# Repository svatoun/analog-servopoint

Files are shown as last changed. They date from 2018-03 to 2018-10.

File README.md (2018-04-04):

# analog-servopoint

Analog-servopoint je zařízení určené k ovládání servo a spínaných (zap/vyp) výstupů pro analogově řízený model železnice. Základní deska má tyto vstupy a výstupy:

1. Vstup z maticové klávesnice 4x4 tlačítek. Funguje jak pro spínací mžiková tlačítka, tak pro přepínací tlačítka. U přepínacích tlačítek může mít význam přepnutí do obou poloh.
2. Ovládání až 8 modelářských serv. 
3. 8 tranzistorem spínaných výstupů, zatížení cca 500mA/výstup, celkem 2,5A

Software poskytuje následující funkce:

### Ovládání serva
1. Určení 2 poloh (levá, pravá) pro každé servo.
2. Určení rychlosti přestavování serva.
3. Interaktivní kalibrace serva
4. Plynulé přestavení serva do předdefinované pravé/levé polohy, nebo na libovolný úhel
5. Postupné spínaní serv, eliminaci proudové špičky, omezení zákmitu serva
6. "Ohlas" polohy serva na definovaném spínaném výstupu (ON/OFF)
7. Přestavování 2 serv najednou

### Ovládání jednotlivých výstupů
1. Zapnutí, vypnutí
2. Pulz 300ms, nebo zadané délky
3. (stále ve vývoji) Blikání s určenou dobou zapnutí a prodlevy. Blikání v protifázi.
4. Napájení tranzistorového pole lze volit jumperem, +5V nebo napětí zdroje.

### Reakce na tlačítka
Tlačítka se čtou po sloupcích, v případě přepinačů je nutné zařadit do matice diody.
1. Přiřazení sekvencí pokynů pro serva a spínané výstupy (max 10 akcí)
2. Spuštění sekvence při stisku, rozepnutí tlačítka nebo obojím
3. Vyčkání přestavení serva, nebo provedení několika akcí najednou
4. Při rozepnutí tlačítka je možné celou posloupnost akcí vrátit nebo přerušit
5. Volitelné prodlevy mezi akcemi
6. Postupné vykonání akcí pro tlačítka stisknutá najednou či v těsném sledu (max 20)

### Nastavení, komunikace
1. Deska se nastavuje a může komunikovat pomocí mikroUSB rozhraní Arduina. 
2. Je možné přímo přikazovat jednotlivé akce (spínání, nastavení serva)
3. Jednoduchý textový výpis konfigurace pro zálohování
4. Upgrade obslužného SW - pomocí Arduino IDE

Podrobnosti viz [Wiki](https://github.com/svatoun/analog-servopoint/wiki/)

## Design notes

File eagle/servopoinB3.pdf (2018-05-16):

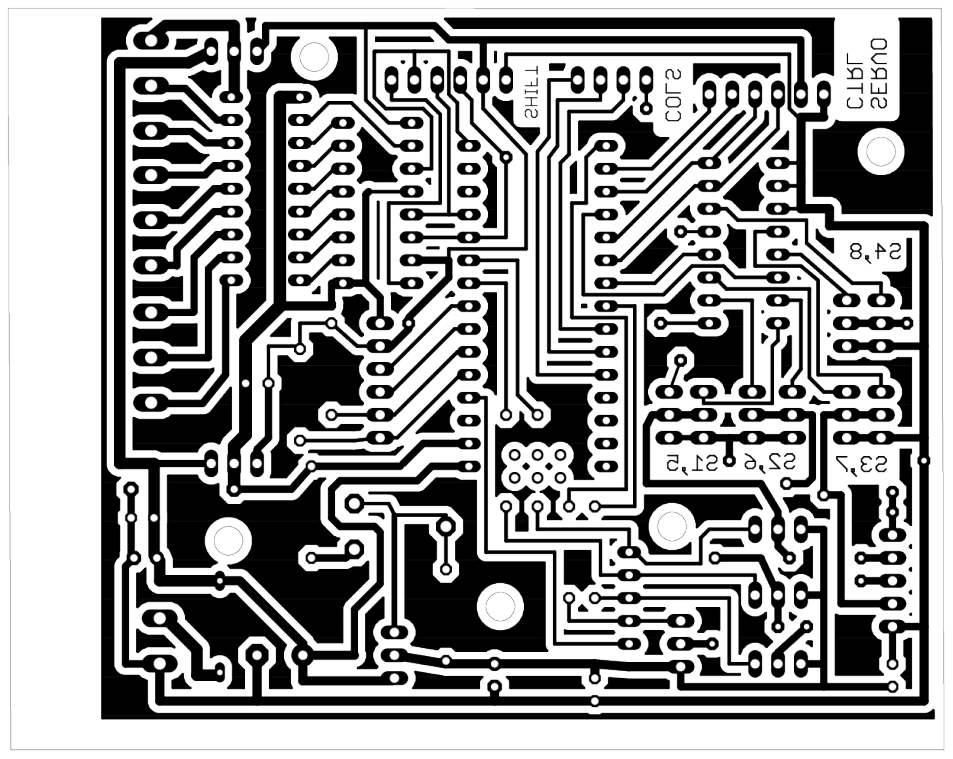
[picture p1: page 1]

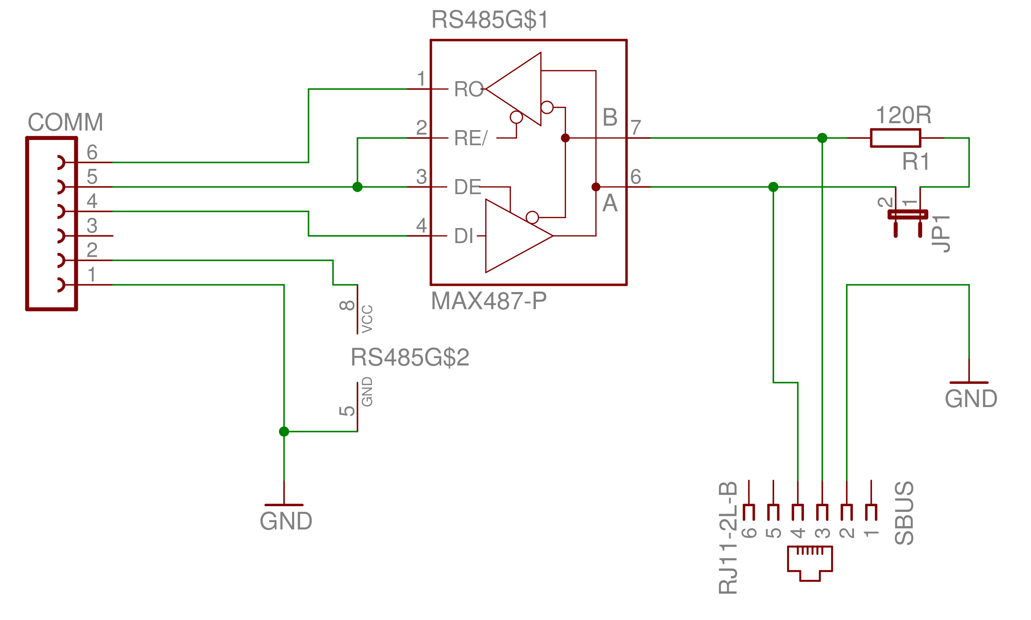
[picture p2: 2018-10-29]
eagle/tco-commheader-pins-schema.png

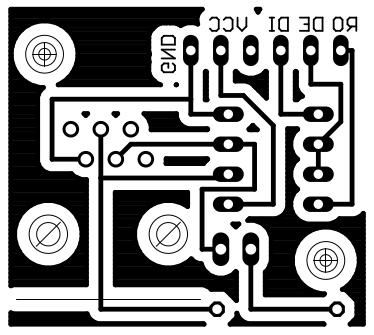
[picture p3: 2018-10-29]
eagle/tco-commheader-pins.png

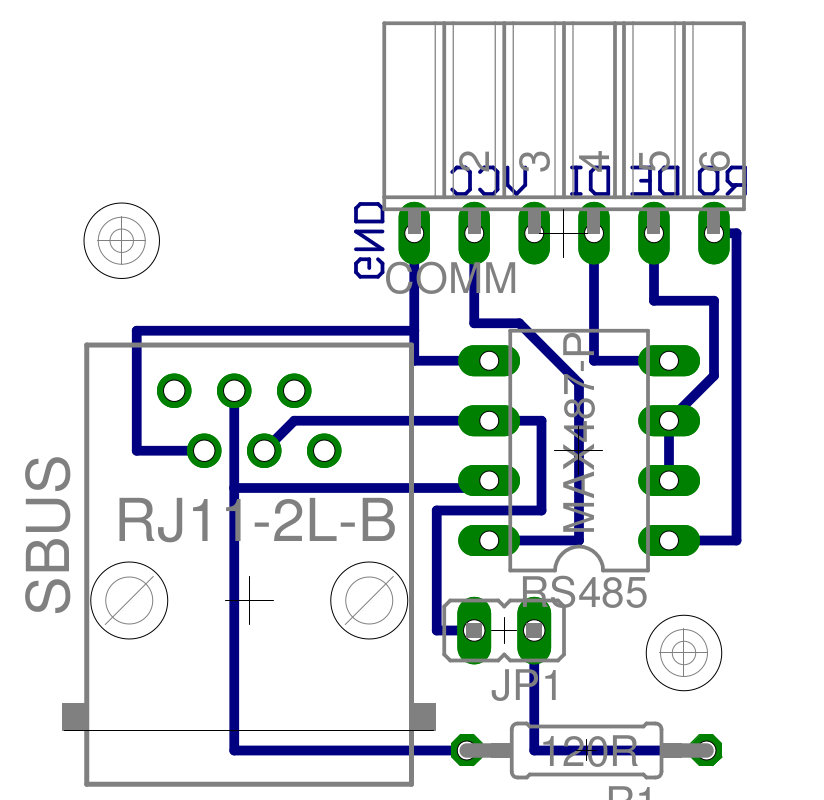
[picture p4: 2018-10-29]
eagle/tco-commheader-pins-osaz.png

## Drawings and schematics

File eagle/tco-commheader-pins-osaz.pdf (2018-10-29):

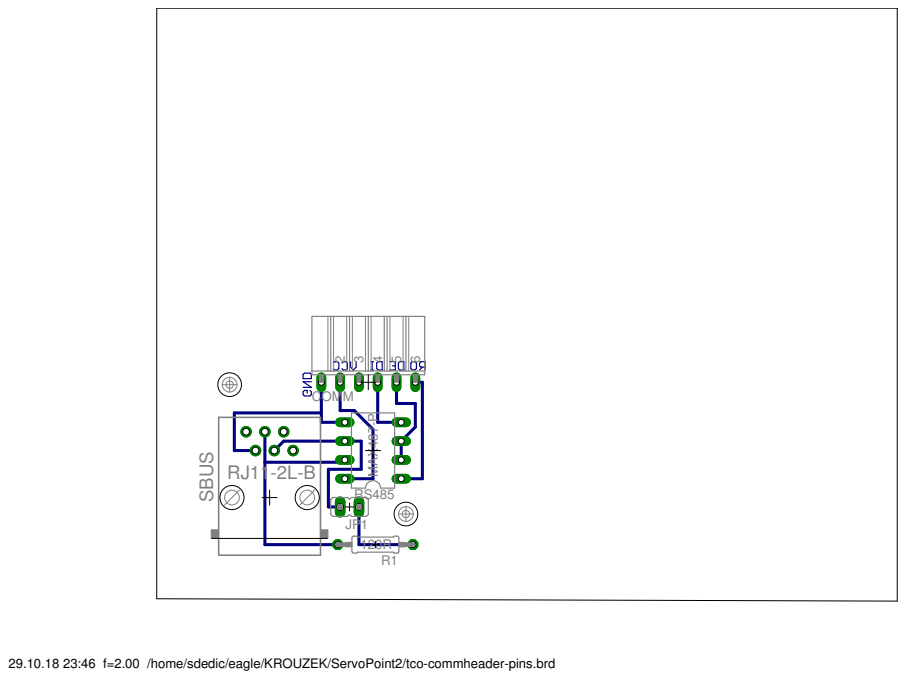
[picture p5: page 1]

29.10.18 23:46 f=2.00 /home/sdedic/eagle/KROUZEK/ServoPoint2/tco-commheader-pins.brd

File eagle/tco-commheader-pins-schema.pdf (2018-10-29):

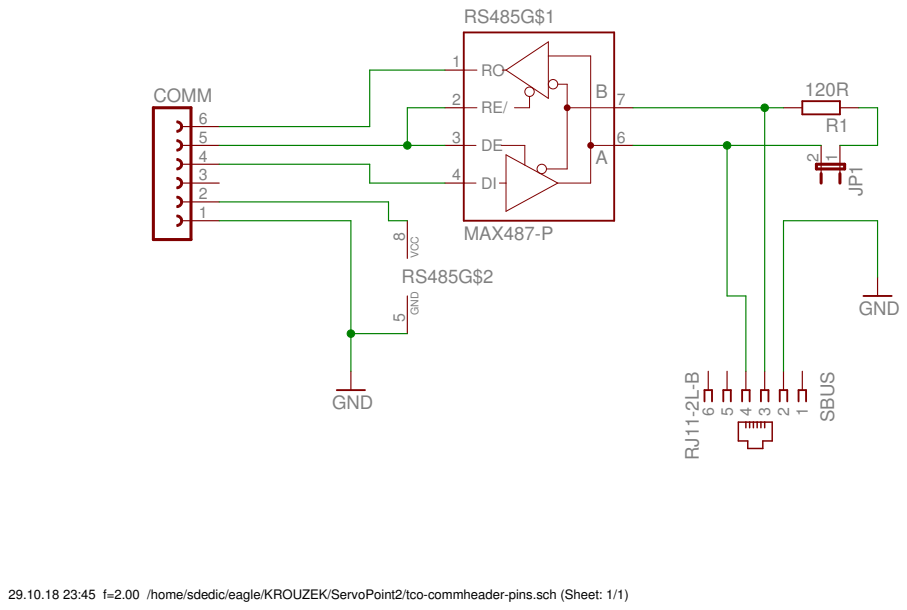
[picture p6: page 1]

29.10.18 23:45 f=2.00 /home/sdedic/eagle/KROUZEK/ServoPoint2/tco-commheader-pins.sch (Sheet: 1/1)

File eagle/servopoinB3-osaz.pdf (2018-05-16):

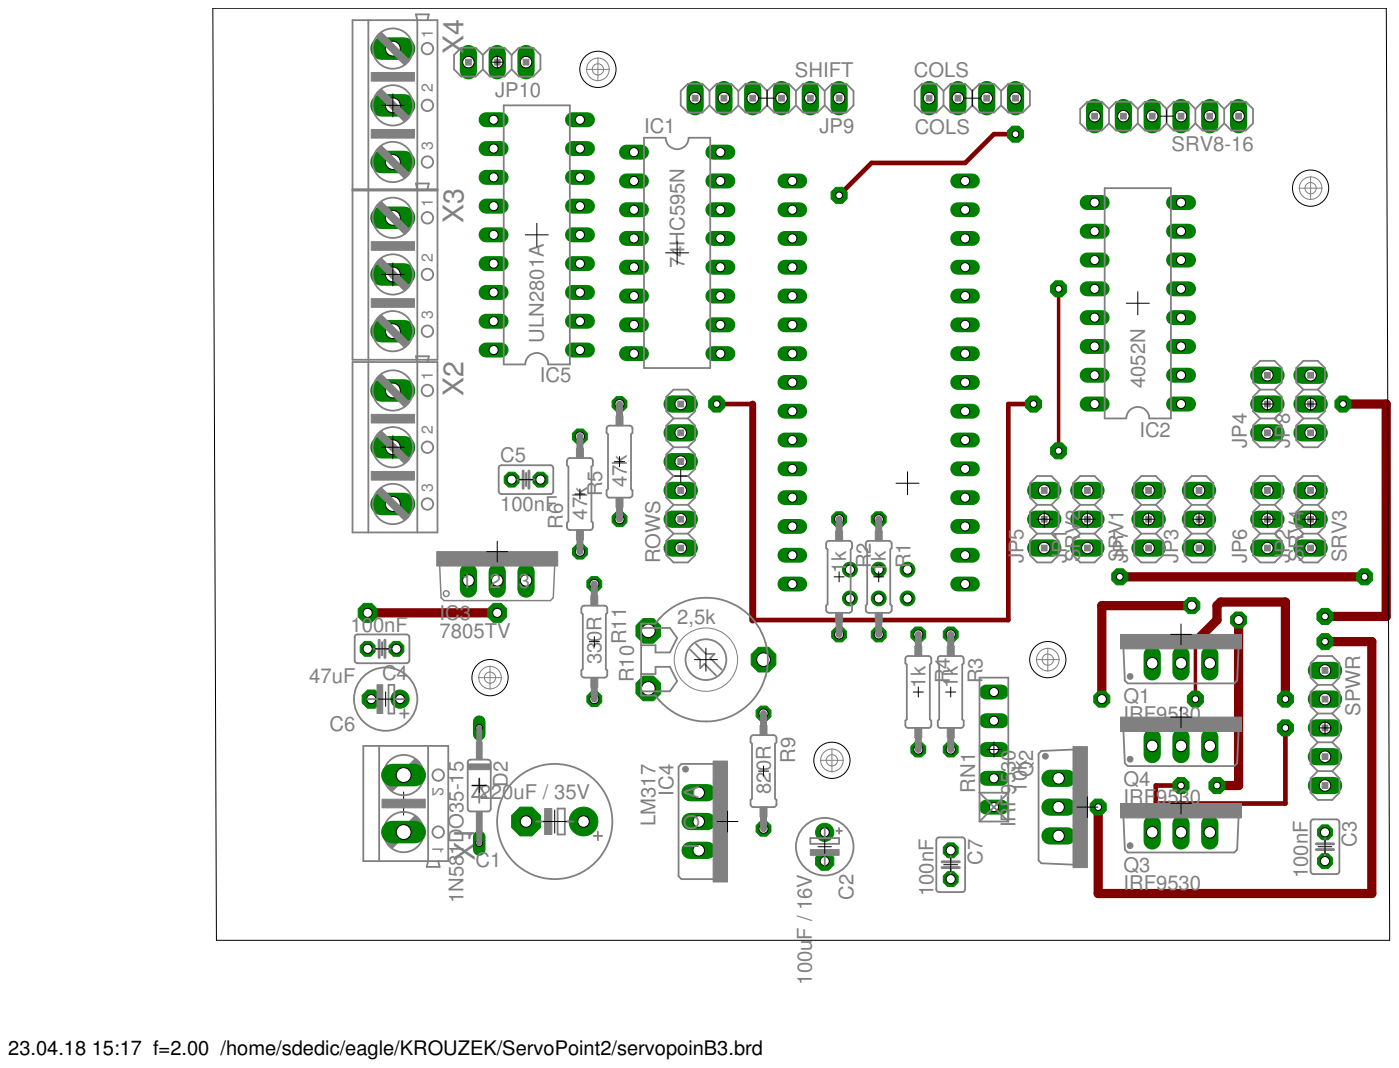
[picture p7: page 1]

23.04.18 15:17 f=2.00 /home/sdedic/eagle/KROUZEK/ServoPoint2/servopoinB3.brd

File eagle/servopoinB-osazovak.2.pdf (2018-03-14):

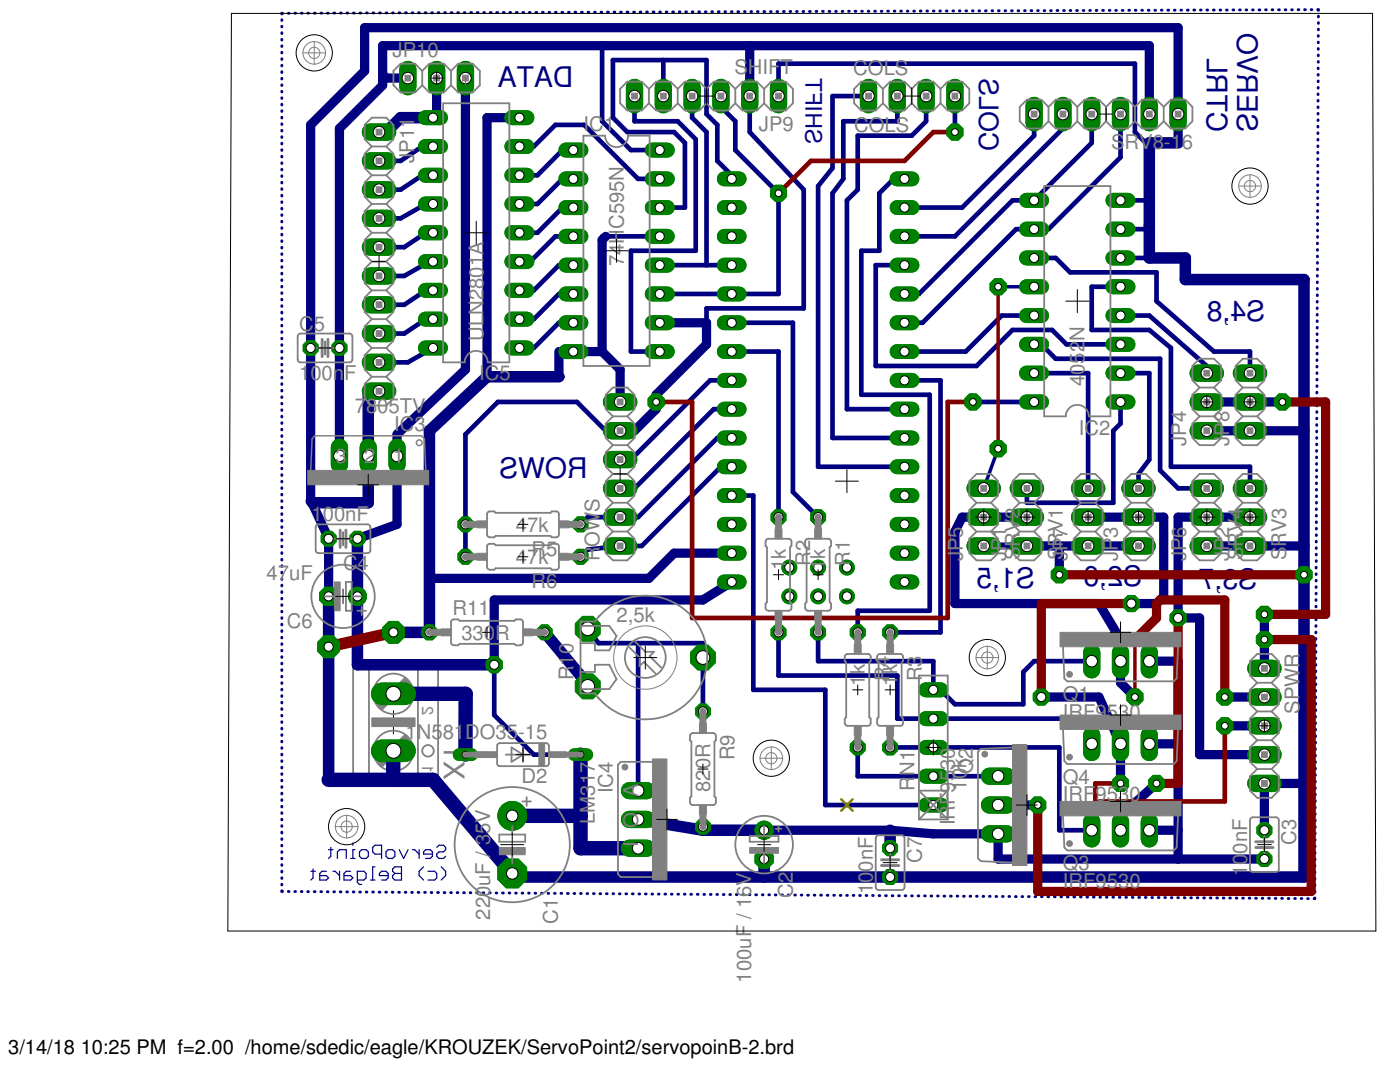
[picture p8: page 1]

3/14/18 10:25 PM f=2.00 /home/sdedic/eagle/KROUZEK/ServoPoint2/servopoinB-2.brd

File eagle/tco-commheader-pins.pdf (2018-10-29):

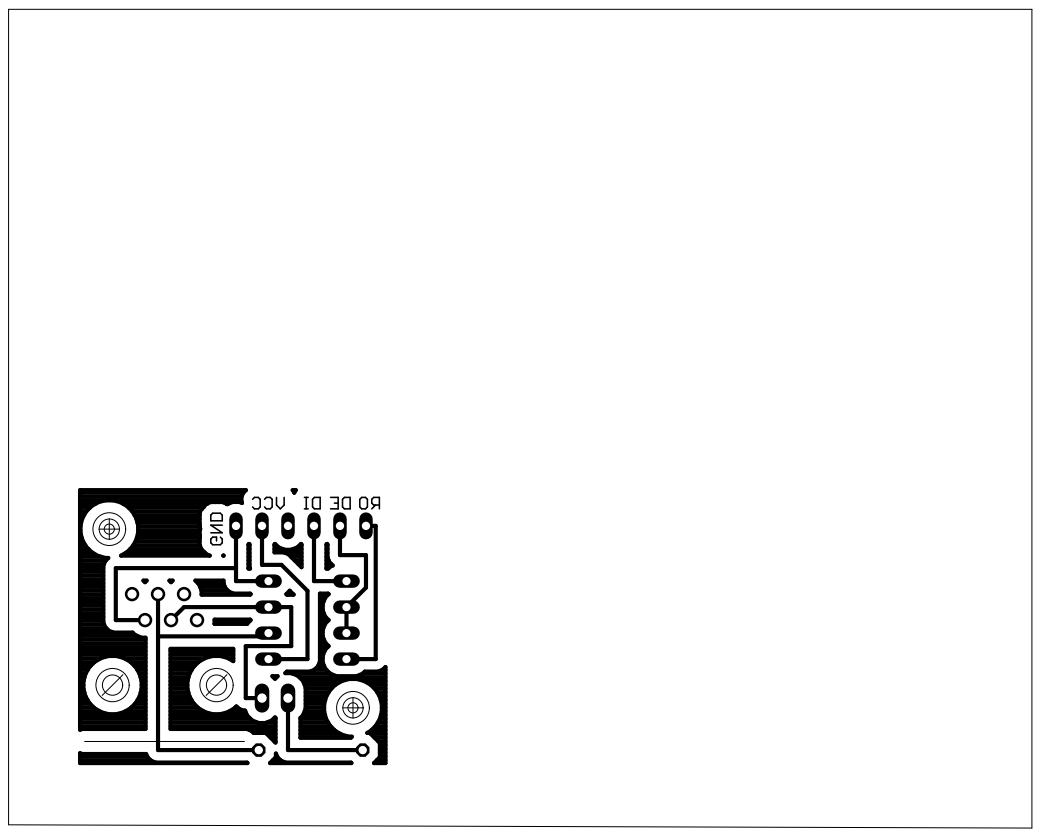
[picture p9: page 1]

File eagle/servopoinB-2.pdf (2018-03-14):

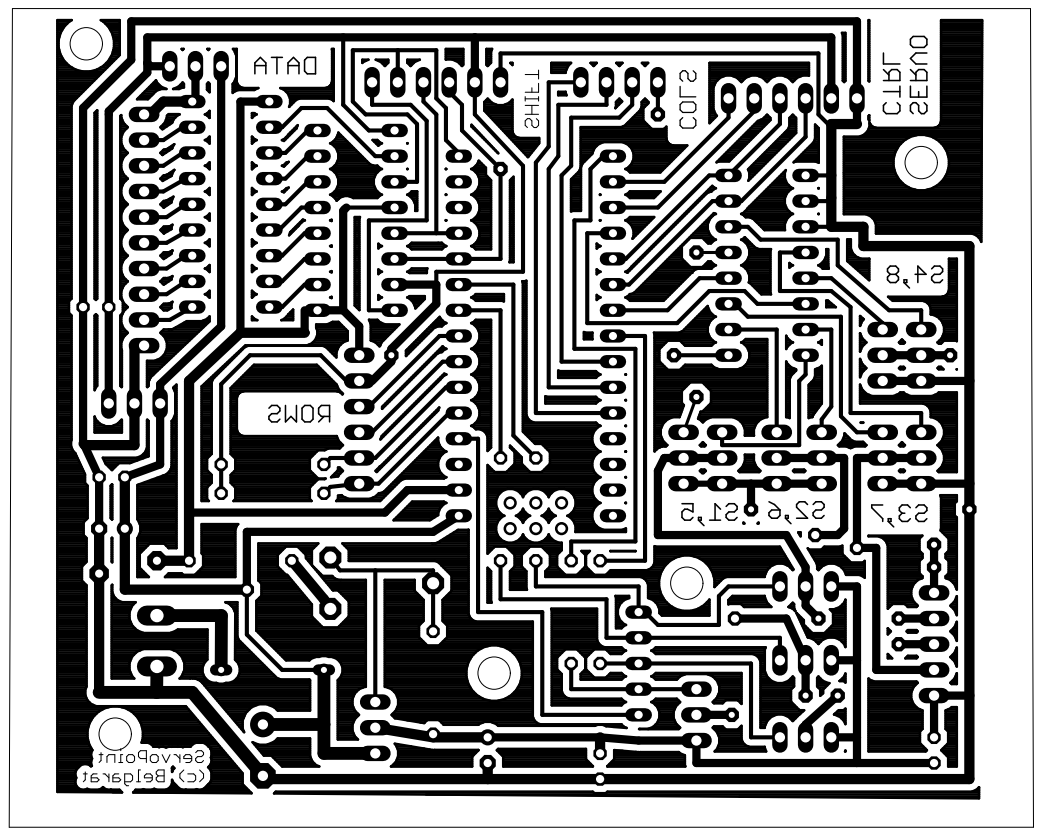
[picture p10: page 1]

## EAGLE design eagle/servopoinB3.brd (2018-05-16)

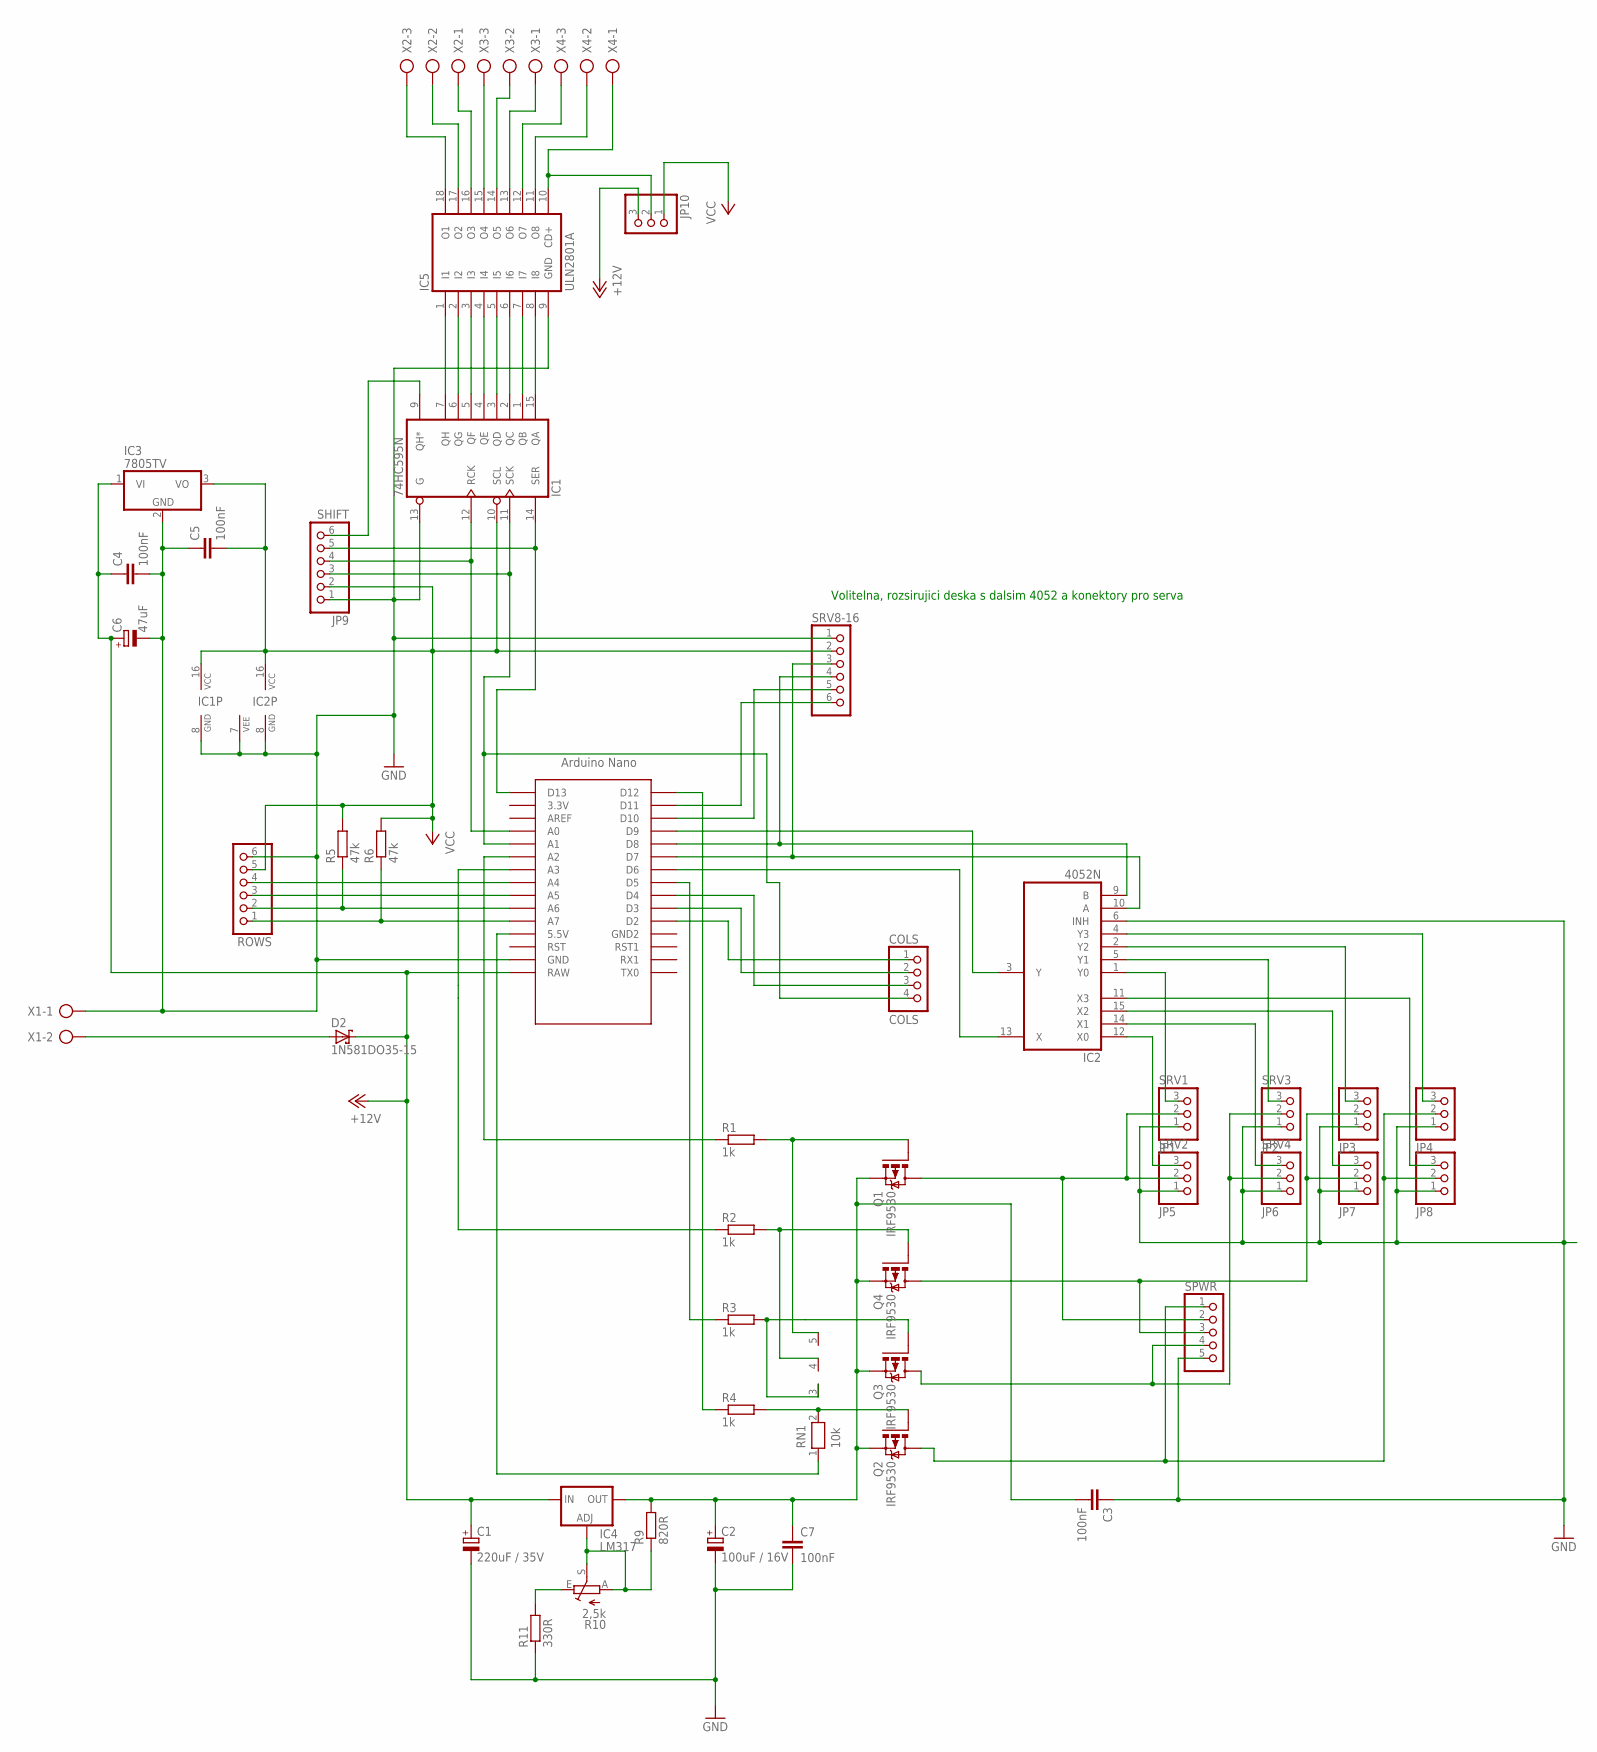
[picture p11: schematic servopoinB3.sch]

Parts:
C1: 220uF / 35V; E5-10,5
C2: 100uF / 16V; E2,5-5
C3, C4, C5, C7: 100nF; C025-025X050
C6: 47uF; E2,5-6
COLS: COLS; 1X04
D2: 1N581DO35-15; DO35-10
IC1: 74HC595N; DIL16
IC2: 4052N; DIL16
IC3: 7805TV; TO220V
IC4: LM317; 317TS
IC5: ULN2801A; DIL18
JP1: SRV1; 1X03
JP2: SRV3; 1X03
JP3, JP4, JP7, JP8, JP10: PINHD-1X3; 1X03
JP5: SRV2; 1X03
JP6: SRV4; 1X03
JP9: SHIFT; 1X06
Q1, Q2, Q3, Q4: IRF9530; TO220BV
R1, R2, R3, R4: 1k; 0207/10
R5, R6: 47k; 0207/10
R9: 820R; 0207/10
R10: 2,5k; LI10
R11: 330R; 0207/10
RN1: 10k; RN-5
ROWS: PINHD-1X6; 1X06
SPWR: PINHD-1X5; 1X05
SRV8-16: PINHD-1X6; 1X06
U$1: NANO
X1: AK500/2
X2, X3, X4: AK500/3

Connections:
+12V: C1.+, C4.1, C6.+, D2.C, IC3.1 (VI), IC4.3 (IN), JP10.3, U$1.RAW
GND: C1.-, C2.-, C3.1, C4.2, C5.1, C6.-, C7.2, IC1.8 (GND), IC1.13 (G), IC2.6 (INH), IC2.7 (VEE), IC2.8 (GND), IC3.2 (GND), IC5.9 (GND), JP1.1, JP2.1, JP3.1, JP4.1, JP5.1, JP6.1, JP7.1, JP8.1, JP9.1, R11.1, ROWS.6, SPWR.5, SRV8-16.1, U$1.GND, X1.1
unnamed: IC2.13 (X), U$1.D6
unnamed: IC2.3 (Y), U$1.D9
unnamed: IC1.15 (QA), IC5.8 (I8)
unnamed: COLS.4, IC1.11 (SCK), JP9.3, U$1.A1
unnamed: IC2.12 (X0), JP5.3
unnamed: IC2.1 (Y0), JP1.3
unnamed: IC2.14 (X1), JP6.3
unnamed: IC2.5 (Y1), JP2.3
unnamed: IC2.15 (X2), JP7.3
unnamed: IC2.2 (Y2), JP3.3
unnamed: IC2.11 (X3), JP8.3
unnamed: IC2.4 (Y3), JP4.3
unnamed: Q1.G, R1.2, RN1.5
unnamed: JP2.2, JP6.2, Q3.D, SPWR.4
unnamed: R6.1, ROWS.1, U$1.A7
unnamed: R2.1, U$1.A3
unnamed: Q4.G, R2.2, RN1.4
unnamed: R3.1, U$1.D5
unnamed: Q3.G, R3.2, RN1.3
unnamed: RN1.1, U$1.5V (5.5V)
unnamed: Q2.G, R4.2, RN1.2
unnamed: JP3.2, JP7.2, Q4.D, SPWR.3
unnamed: R4.1, U$1.D12
unnamed: R1.1, U$1.A2
unnamed: D2.A, X1.2
unnamed: ROWS.4, U$1.A4
unnamed: ROWS.3, U$1.A5
unnamed: R5.1, ROWS.2, U$1.A6
unnamed: SRV8-16.6, U$1.D11
unnamed: COLS.2, U$1.D3
unnamed: COLS.3, U$1.D4
unnamed: COLS.1, U$1.D2
unnamed: SRV8-16.5, U$1.D10
unnamed: IC1.14 (SER), JP9.5, U$1.D13
unnamed: IC1.1 (QB), IC5.7 (I7)
unnamed: IC1.9 (QH*), JP9.6
unnamed: IC1.12 (RCK), JP9.4, U$1.A0
unnamed: C2.+, C3.2, C7.1, IC4.2 (OUT), Q1.S, Q2.S, Q3.S, Q4.S, R9.2
unnamed: IC5.10 (CD+), JP10.2, X4.1
unnamed: IC1.2 (QC), IC5.6 (I6)
unnamed: IC1.3 (QD), IC5.5 (I5)
unnamed: IC1.4 (QE), IC5.4 (I4)
unnamed: IC1.5 (QF), IC5.3 (I3)
unnamed: IC1.6 (QG), IC5.2 (I2)
unnamed: IC1.7 (QH), IC5.1 (I1)
unnamed: IC5.18 (O1), X2.3
unnamed: IC4.1 (ADJ), R9.1, R10.A, R10.S
unnamed: R10.E, R11.2
unnamed: IC5.17 (O2), X2.2
unnamed: JP1.2, JP5.2, Q1.D, SPWR.2
unnamed: IC5.16 (O3), X2.1
unnamed: JP4.2, JP8.2, Q2.D, SPWR.1
unnamed: IC5.15 (O4), X3.3
unnamed: IC5.14 (O5), X3.2
unnamed: IC5.13 (O6), X3.1
unnamed: IC5.12 (O7), X4.3
unnamed: IC5.11 (O8), X4.2
unnamed: IC2.9 (B), SRV8-16.4, U$1.D8
unnamed: IC2.10 (A), SRV8-16.3, U$1.D7
VCC: C5.2, IC1.10 (SCL), IC1.16 (VCC), IC2.16 (VCC), IC3.3 (VO), JP9.2, JP10.1, R5.2, R6.2, ROWS.5, SRV8-16.2

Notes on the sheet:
Volitelna, rozsirujici deska s dalsim 4052 a konektory pro serva

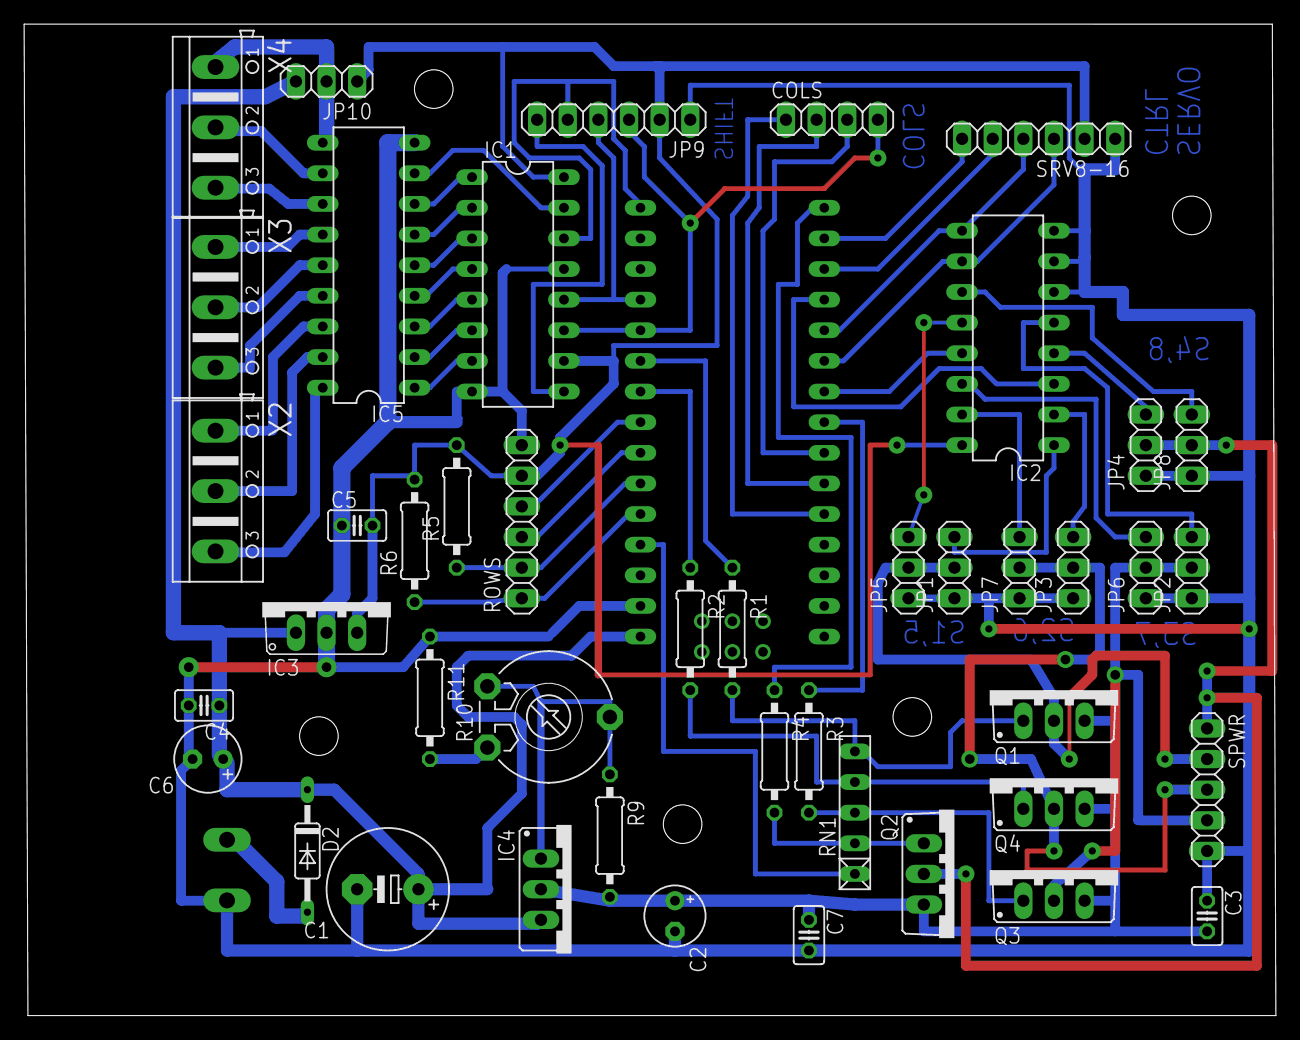
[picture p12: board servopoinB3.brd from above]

Board: 2 copper layers, 103.8 x 82.2 mm, 46 parts (1 on the bottom side), 62 nets.

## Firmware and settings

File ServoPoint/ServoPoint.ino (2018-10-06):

#ifdef NEO
#include <NeoSWSerial.h>
#else
#include <SoftwareSerial.h>
#endif

#include "RS485Frame.h"
#undef SOFTWARE_SERVO

#define DEBUG

#include <EEPROM.h>

#ifdef SOFTWARE_SERVO
#include <SoftwareServo.h>
#define Servo SoftwareServo
#else 
#include <Servo.h>
#endif

#include "Common.h"

ModuleChain* ModuleChain::head;

byte keyStateTriggered[(maxId + 7) / 8];
byte keyState[(maxId + 7) / 8];

Command commands[MAX_COMMANDS];

char printBuffer[50];

/**
   Serves to build up a new command during setup. Takes priority over any actions
*/
Action  newCommand[newCommandPartMax];


//ModuleChain *modules;

/**
   The current number of milliseconds; read at the start of the loop().
*/
long currentMillis;

Output output;
Executor executor;

char currentKey;
uint8_t * heapptr, * stackptr;
/*
void check_mem() {
  stackptr = (uint8_t *)malloc(4);          // use stackptr temporarily
  heapptr = stackptr;                     // save value of heap pointer
  free(stackptr);      // free up the memory again (sets stackptr to 0)
  stackptr =  (uint8_t *)(SP);           // save value of stack pointer
}
*/

int freeRam ()
{
  extern int __heap_start, *__brkval;
  int v;
  return (int) &v - (__brkval == 0 ? (int) &__heap_start : (int) __brkval);
}

void clearNewCommand() {
//  check_mem();
  if (debugControl) {
    Serial.println(F("Clearing new command"));
  }
  executor.clear(true);
  for (Action* a = newCommand; a < (newCommand + newCommandPartMax); a++) {
    a->init();
  }
}

int addNewCommand(const Action& t) {
  if (debugControl) {
    Serial.print(F("Adding action command "));
    Serial.print(F("Source: ")); Serial.print((int)&t, HEX);
    Serial.print(t.command);
    Serial.print(F(", data = "));
    Serial.println(t.data, HEX);
  }
  Action* prev = newCommand;
  for (Action* pa = newCommand; pa < (newCommand + newCommandPartMax); pa++) {
    Action& a = *pa;
    if (a.isEmpty()) {
      a = t;
      if (debugControl) {
        Serial.print(F("Added at position"));
        Serial.print((pa - newCommand));
        Serial.print(F(" = "));
        Serial.print((int)&a, HEX);
        Serial.print(F(":"));
        Serial.print(a.command);
        Serial.print(F(", data = "));
        Serial.println(a.data, HEX);
      }
      prev->notLast();
      a.makeLast();
      return (pa - newCommand);
    }
  }
  return -1;
}


////////////////////////////////////////////////////////////////////////////////////////////////////////////////////
// ACK / status LED handling
const int* blinkPtr = NULL;
long blinkLastMillis;
byte pos = 0;
boolean ackLedState = false;
byte pulseCount = 0;

const int blinkShort[] = { 250, 250, 0 };   // blink once, short
const int blinkLong[] = { 500, 0 };
const int blinkReject[] = { 250, 250, 250, 250, 0 };
const int blinkSave[] = { 250, 250, 250, 250, 250, 250, 500, 0 };


void makeLedAck(const int *  ledSequence) {
  blinkPtr = ledSequence;
  pos = 0;
  ackLedState = 1;
  blinkLastMillis = millis();
  digitalWrite(LED_ACK, HIGH);
  if (debugControl) {
    Serial.print(F("LED ACK: ")); Serial.println(blinkPtr[pos]);
  }
}

void handleAckLed() {
  if (blinkPtr == NULL) {
    return;
  }
  long t = millis();
  long l = t - blinkLastMillis;
  if (l < *blinkPtr) {
    return;
  }
  blinkLastMillis = t;
  blinkPtr++;
  if (debugControl) {
    Serial.print(F("Next ACK time: ")); Serial.println(*blinkPtr);
  }
  if (*blinkPtr == 0) {
    ackLedState = 0;
    digitalWrite(LED_ACK, LOW);
    if (pulseCount > 0) {
      pulseCount--;
      makeLedAck(&blinkShort[0]);
    } else {
      if (debugControl) {
        Serial.println(F("ACK done"));
      }
      blinkPtr = NULL;
      blinkLastMillis = -1;
    }
    return;
  }
  ackLedState = !ackLedState;
  digitalWrite(LED_ACK, ackLedState ? HIGH : LOW);
}

//////////////////////////////////////////////////////////////////////////

void initializeHW() {
    Serial.begin(115200);
//  Serial.begin(57600);
  // put your setup code here, to run once:
  pinMode(LED_ACK, OUTPUT);
  digitalWrite(LED_ACK, LOW);
  analogReference(DEFAULT);

  Serial.println(COPYRIGHT);
}

void checkInitEEPROM() {
  int savedVer = EEPROM.read(eeaddr_version);
  if (savedVer == CURRENT_DATA_VERSION) {
    return;
  }
  Serial.println(F("Obsolete EEPROM, reinitializing"));
  ModuleChain::invokeAll(ModuleCmd::reset);
  ModuleChain::invokeAll(ModuleCmd::eepromSave);
  EEPROM.write(eeaddr_version, CURRENT_DATA_VERSION);
}

void setup() {
  initializeHW();
  checkInitEEPROM();

  bootProcessors();
  
  ModuleChain::invokeAll(ModuleCmd::initialize);
  
  //  initializeTables();
  for (int i = 0; i < sizeof(keyState); i++) {
    keyState[i] = 0;
    keyStateTriggered[i] = 0;
  }

  // initial load of key / switch positions
//  enterSetup();

  Serial.print(F("Size of commands: ")); Serial.println(sizeof(commands));
  Serial.print(F("Size of executors: ")); Serial.println(sizeof(Executor) + sizeof(ServoProcessor));
  Serial.print(F("Size of actions: ")); Serial.println(sizeof(Action) * MAX_ACTIONS);

  registerLineCommand("SAV", &saveHandler);

  printPrompt();
}

/**
   Writes a block of data into the EEPROM, followed by a checksum
*/
void eeBlockWrite(byte magic, int eeaddr, const void* address, int size) {
  if (debugControl) {
    Serial.print(F("Writing EEPROM ")); Serial.print(eeaddr, HEX); Serial.print(F(":")); Serial.print(size); Serial.print(F(", source: ")); Serial.println((int)address, HEX);
  }
  const byte *ptr = (const byte*) address;
  byte hash = magic;
  EEPROM.write(eeaddr, magic);
  eeaddr++;
  for (; size > 0; size--) {
    byte b = *ptr;
    EEPROM.write(eeaddr, b);
    ptr++;
    eeaddr++;
    hash = hash ^ b;
  }
  EEPROM.write(eeaddr, hash);
}

/**
   Reads block of data from the EEPROM, but only if the checksum of
   that data is correct.
*/
boolean eeBlockRead(byte magic, int eeaddr, void* address, int size) {
  if (debugControl) {
    Serial.print(F("Reading EEPROM ")); Serial.print(eeaddr, HEX); Serial.print(F(":")); Serial.print(size); Serial.print(F(", dest: ")); Serial.println((int)address, HEX);
  }
  int a = eeaddr;
  byte hash = magic;
  byte x;
  boolean allNull = true;
  x = EEPROM.read(a);
  if (x != magic) {
    if (debugControl) {
      Serial.println(F("No magic header found"));
    }
    return false;
  }
  a++;
  for (int i = 0; i < size; i++, a++) {
    x = EEPROM.read(a);
    if (x != 0) {
      allNull = false;
    }
    hash = hash ^ x;
  }
  x = EEPROM.read(a);
  if (hash != x || allNull) {
    if (debugControl) {
      Serial.println(F("Checksum does not match"));
    }
    return false;
  }

  a = eeaddr + 1;
  byte *ptr = (byte*) address;
  for (int i = 0; i < size; i++, a++) {
    x = EEPROM.read(a);
    *ptr = x;
    ptr++;
  }
}

void primeKeyChange(byte k) {
  if (k >= maxId) {
    return;
  }
  bitfieldWrite(keyStateTriggered, k, true); 
}

char getKeyChange(byte k) {
  if (k >= maxId) {
    return -1;
  }
  if (bitfieldRead(keyStateTriggered, k)) {
    return -1;
  }
  return bitfieldRead(keyState, k) ? 1 : 0;
}

bool isKeyPressed(byte k) {
  if (k >= maxId) {
    return false;
  }
  return bitfieldRead(keyState, k);
}

bool setKeyPressed(int k, bool val) {
  bitfieldWrite(keyState, k, val);
  bitfieldWrite(keyStateTriggered, k, false);
}

void processKey(int k, boolean pressed) {
  setKeyPressed(k, pressed);
  Command::processAll(k, pressed);
}

/*
void processKeyCallback(const Key2& k, char c) {
    if (setupActive) {
      return;
    }
    if (debugInput) {
      Serial.println(F("Key state changed"));
    }
    if (k.kstate == IDLE || k.kstate == HOLD) {
      // ignore hold / idle
      return;
    }
    boolean pressed = (k.kstate  == PRESSED);
    int ch = keypad.getChar(k);
    Serial.print(F("Processing key: #")); Serial.print(ch);
    if (pressed) {
      Serial.println(F(" DOWN"));
    } else {
      Serial.println(F(" UP"));
    }
    processKey(ch - 1, pressed);
}
*/

void loop() {
  currentMillis = millis();
  // pressedKey = keypad.getKey();

  if (setupActive) {
    setupLoop();
  }
  scheduler.schedulerTick();
  handleAckLed();
  executor.process();
  ModuleChain::invokeAll(ModuleCmd::periodic);
  // explicit, at the end
  output.commit();
  processReceivedCommand();
}


const int blinkSetup[] = { 500, 250, 500, 250, 500, 250, 0 };
const int blinkError[] = { 1000, 250, 1000, 250, 0 };


void saveHandler() {
  ModuleChain::invokeAll(ModuleCmd::eepromSave);
}

int defineCommand(const Command& def, int no) {
  if (no >= 0) {
    if (no >= MAX_COMMANDS) {
      return -1;
    }
  } else {
    for (const Command* ptr = commands; ptr < commands + MAX_COMMANDS; ptr++) {
      if (ptr->available()) {
        no = (ptr - commands);
        break;
      }
    }
  }
  if (no == -1) {
    if (debugCommands) {
      Serial.println(F("No free slots"));
    }
    return -1;
  }
  Command& c = commands[no];
  if (!c.available()) {
      if (debugCommands) {
        Serial.print(F("Existing command ")); Serial.println(no);
      }
      replaceCommand(c, def);
      return no;
  } else {
    return defineNewCommand(def, c);
  }  
}

int defineNewCommand(const Command& c, Command& target) {
  boolean empty = true;
  boolean ok = false;
  Action* pa;
  for (pa = newCommand; pa < (newCommand + newCommandPartMax); pa++) {
    Action& a = *pa;
    if (a.isEmpty()) {
      pa--;
      ok = true;
      break;
    }
    empty = false;
    if (a.isLast()) {
      ok = true;
      break;
    }
  }
  if (empty || !ok) {
    return -1;
  }
  pa->makeLast();
  int s = (pa - newCommand) + 1;
  if (debugCommands) {
    Serial.print(F("Action count: ")); Serial.println(s);
  }
  int aIndex = Action::copy(&newCommand[0], s);
  if (debugCommands) {
    Serial.print(F("Copied at: ")); Serial.println(aIndex);
  }
  target = c;
  target.actionIndex = aIndex;
  return &target - commands;
}

boolean deleteCommand(int i) {
  if (i < 0 || i >= MAX_COMMANDS) {
    return false;
  }
  Command &c = commands[i];
  if (c.available()) {
    return false;
  }
  c.free();
  return true;
}

void replaceCommand(Command& c, const Command& def) {
  c.free();
  defineNewCommand(def, c);
}

ModuleChain::ModuleChain(const char* name, byte aPrirority,  void (*h)(ModuleCmd)) : next(NULL), priority(aPrirority) {
  static ModuleChain* __last = NULL;
  if (__last == NULL) {
    head = NULL;
  }
  __last = this;
  handler = h;
  if (head == NULL) {
    head = this;
    return;
  }
  if (head->priority >= aPrirority) {
    next = head;
    head = this;
    return;
  }
  ModuleChain* p = head;
  while (p->priority < aPrirority) {
    if (p->next == NULL) {
      p->next = this;
      return;
    }
    p = p->next;
  }
  if (p->next == NULL) {
    p->next = this;
    return;
  }
  next = p->next;
  p->next = this;
}

void ModuleChain::invokeAll(ModuleCmd cmd) {
  ModuleChain*p = head;
  while (p != NULL) {
    if (p->handler != NULL) {
      p->handler(cmd);
    }
    p = p->next;
  }
}

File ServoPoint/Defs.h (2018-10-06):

#ifndef __defs_h__
#define __defs_h__

#define SERVOS

/**
 * Velikost prijmoveho bufferu v byte. Musi byt delsi nez nejdelsi zpracovavany packet.
 * Delsi packety se ani nezaznamenavaji a zahazuji rovnou.
 */
const int recvBufferSize = 11;

const int ROWS = 4;
const int COLS = 4;

#define COPYRIGHT F("ServoPoint v2.0/Xbus, Copyright(c) 2018, Belgarat@klfree.net")

//------------------------------- PIN ASSIGNMENT ------------------------------------
/**
 * ACK LED, will blink in response to setup keypresses
 * and status
 */
const int LED_ACK = 13;

const int rs485Receive = 2;
const int rs485Send = 4;
const int rs485Direction = 3;

const int latchPin  = A0;
const int clockPin  = A1;
const int dataPin   = 13;
//const int shiftOutDisable = 12;

// A0 .. A5 (6x), D2, D3, D6 = keypad, 20 klaves
// D7, D8, D9 = seriove rizeni vystupu
// D4, D5 = I2C komunikace
// D11 - PWM pro serva
// zbyva: D10, D12, D13
// zbyva: A6, A7

const int pwmPinA = 6;
const int pwmPinB = 9;

const int servoSelectA = 7;
const int servoSelectB = 8;
//const int servo18Enable = 12;

const int servoPowerA = A2;
const int servoPowerB = 5;
const int servoPowerC = A3;
const int servoPowerD = 12;

#define SHIFTPWM_PHYSICAL_PINS
#define PORT_LATCH  PC
#define BIT_LATCH 0

#define PORT_DATA PB
#define BIT_DATA 5

#define PORT_CLOCK PC 
#define BIT_CLOCK 1

//------------------------------- END PIN ASSIGNMENT ------------------------------------

const int maxId = ROWS * COLS;

const int QUEUE_SIZE = 10;          // # of parallel executions
const int MAX_ACTIONS = 128;        // # of possible actions
const int MAX_COMMANDS = 32;        // # of defined commands
const int MAX_WAIT_COUNT = 10;      // # of suspended executions
const int MAX_SERVO = 16;           // # of controlled servos
const int MAX_OUTPUT = 64;          // # of on/off outputs from the shift register
const int MAX_INPUT_BUTTONS = 16;   // # of input buttons
const int MAX_SPEED = 8;            // servo speed
const int MAX_FLASH = 4;

const int MAX_SCHEDULED_ITEMS = 16;
const int MAX_PENDING_FLASHES = 8;

const int MAX_KEYS = (ROWS * COLS);
const int OUTPUT_BIT_SIZE = (MAX_OUTPUT + 7) / 8;
const int SERVO_BIT_SIZE = (MAX_SERVO + 7) / 8;
const int COMMAND_BIT_SIZE = (MAX_COMMANDS + 7) / 8;

const int defaultPulseDelay = 100;

/**
 * Maximum number of processors. Each servo processor counts as 1 !
 */
const int MAX_PROCESSORS = 20;

#define MILLIS_SCALE_FACTOR 50

/**
 * If != 0, setup control routines will print diagnostic messages over serial line.
 */

#ifdef DEBUG
const int debugControl = 0;
const int debugExecutor = 0;
const int debugServo = 0;
const int debugServoMove = 0;
const int debugOutput = 0;
const int debugCommands = 0;
const int debugInfra = 0;
const int debugInput = 0;
const int debugPower = 0;
const int debugSchedule = 0;
const int debugFlash = 0;
const int debugConditions = 0;
#else
const int debugControl = 0;
const int debugExecutor = 0;
const int debugServo = 0;
const int debugServoMove = 0;
const int debugOutput = 0;
const int debugCommands = 0;
const int debugInfra = 0;
const int debugInput = 0;
const int debugPower = 0;
const int debugSchedule = 0;
const int debugFlash = 0;
const int debugConditions = 0;
#endif

/**
 * Pins controlling the output
 */
const int numberOfLatches   = 1;
static_assert (numberOfLatches <= OUTPUT_BIT_SIZE, "Invalid number of latches");

#endif

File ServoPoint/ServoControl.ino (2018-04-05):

//
///////////////////////////// Servo Movement //////////////////////////////

int overrideSpeed = -1;
extern ServoConfig setupServoConfig;
extern byte setupServoLeft;
extern byte setupServoRight;
extern byte setupServoSpeed;
extern signed char setupServoOutput;

#ifdef SERVOS
ServoProcessor  processors[2];  

/**
   Servo predefined positions.
*/

ModuleChain servoModule("Servo", 0, &servoModuleHandler);

byte servosActiveTrigger[SERVO_BIT_SIZE];
byte servosActive[SERVO_BIT_SIZE];
byte  servoPositions[MAX_SERVO]; 
boolean enable = false;


void primeServoActive(byte k) {
  if (k >= SERVO_BIT_SIZE) {
    return;
  }
  bitfieldWrite(servosActiveTrigger, k, true);
}

bool isServoActive(byte k) {
  if (k >= SERVO_BIT_SIZE) {
    return false;
  }
  return bitfieldRead(activeOutputs, k);
}

char getServoActive(byte k) {
  if (k >= SERVO_BIT_SIZE) {
    return - 1;
  }
  if (bitfieldRead(servosActiveTrigger, k)) {
    return -1;
  }
  return bitfieldRead(activeOutputs, k) ? 1 : 0;
}

boolean setServoActive(byte k, boolean s) {
  if (k >= SERVO_BIT_SIZE) {
    return;
  }
  bitfieldWrite(servosActiveTrigger, k, false);
  bitfieldWrite(activeOutputs, k, s);
}


void ServoConfig::print(byte id, char* out) {
  strcat_P(out, PSTR("RNG:"));
  out += strlen(out);
  out = printNumber(out, id, 10);
  append(out, ':');
  out = printNumber(out, left(), 10);
  append(out, ':');
  out = printNumber(out, right(), 10);
  append(out, ':');
  out = printNumber(out, servoSpeed + 1, 10);
  int p = output();
  if (p == -1) {
    return;
  }
  strcat_P(out, PSTR("\nSFB:"));
  out += strlen(out);
  out = printNumber(out, id, 10);
  append(out, ':');
  printNumber(out, p + 1, 10);
}

void servoSetup() {
  pinMode(servoSelectA, OUTPUT);
  pinMode(servoSelectB, OUTPUT);
//  pinMode(servo18Enable, OUTPUT);

  pinMode(servoPowerA, OUTPUT);
  pinMode(servoPowerB, OUTPUT);
  pinMode(servoPowerC, OUTPUT);
  pinMode(servoPowerD, OUTPUT);

  digitalWrite(servoPowerA, HIGH);
  digitalWrite(servoPowerB, HIGH);
  digitalWrite(servoPowerC, HIGH);
  digitalWrite(servoPowerD, HIGH);

  executor.addProcessor(&processors[0]);
  processors[0].clear();
  executor.addProcessor(&processors[1]);
  processors[1].clear();
  
  processors[0].attach(pwmPinA, 0b01010101);
  processors[1].attach(pwmPinB, 0b10101010);
  processors[0].linkWith(&processors[1]);

  for (int i = 0; i < MAX_SERVO; i++) {
    servoPositions[i] = 90;
  }
  servoEepromLoad();

  if (debugControl) {
    Serial.println(F("Servo config:"));
    servoDump();
    servoStatus();
  }
  startServos1To8();
  // register commands
  registerLineCommand("RNG", &rangeCommand);
  registerLineCommand("MOV", &moveCommand);
  registerLineCommand("CAL", &commandCalibrate);
  registerLineCommand("SFB", &commandServoFeedback);

  Action::registerDumper(servo, printServoAction);

  for (int i = 0; i < sizeof(SERVO_BIT_SIZE); i++) {
    servosActive[i] = 0;
    servosActiveTrigger[i] = 0;
  }
}

void printServoAction(const Action& a, char* out) {
  const ServoActionData& sa = a.asServoAction();
  strcat_P(out, PSTR("MOV:"));
  out += strlen(out);
  out = printNumber(out, sa.servoIndex + 1, 10);
  append(out, ':');
  if (sa.isPredefinedPosition()) {
    append(out, sa.isLeft() ? 'L' : 'R');
    *out = 0;
  } else {
    printNumber(out, sa.targetPosition(), 10);
  }
}

void servoDump() {
  ServoConfig tmp;
  for (int i = 0; i < MAX_SERVO; i++) {
    tmp.load(i);
    if (tmp.isEmpty()) {
      continue;
    }
    initPrintBuffer();
    tmp.print(i + 1, printBuffer);
    Serial.println(printBuffer);
  }
}

void servoClear() {
  for (int i = 0; i < MAX_SERVO; i++) {
    ServoConfig tmp;
    tmp.clear();
    tmp.save(i);
  }
  for (int i = 0; i < sizeof(servoPositions) / sizeof(servoPositions[0]); i++) {
    servoPositions[i] = 90;
  }
}

void servoStatus() {
  int srvCount = 0;
  for (int i = 0; i < MAX_SERVO; i++) {
    ServoConfig tmp;
    tmp.load(i);
    if (tmp.isEmpty()) {
      continue;
    }
    srvCount++;
  }
  Serial.print(F("Servos defined: ")); Serial.println(srvCount);
    Serial.print(F("Servo Positions: "));
    for (int i = 0; i < sizeof(servoPositions) / sizeof(servoPositions[0]); i++) {
      Serial.print((int)servoPositions[i]); Serial.print(F(","));
    }
    Serial.println();
}

void servoModuleHandler(ModuleCmd cmd) {
  switch (cmd) {
    case initialize:
      servoSetup();
      break;
    case eepromLoad:
      servoEepromLoad();
      break;
    case eepromSave:
      servoEEWriteSetup();
      break;
    case dump:
      servoDump();
      break;
    case status:
      servoStatus();
      break;
    case reset:
      servoClear();
      break;
    case periodic:
      handleServoMovement();
      break;
  }
}

void servoEepromLoad() {
//  eeBlockRead('S', eeaddr_servoConfig, &servoConfig[0], sizeof(servoConfig));
  eeBlockRead('P', eeaddr_servoPositions, &servoPositions[0], sizeof(servoPositions));
}

void ServoConfig::load(byte idx) {
  EEPROM.get(eeaddr_servoConfig + idx * sizeof(ServoConfig), *this);
}

void ServoConfig::save(byte idx) {
  EEPROM.put(eeaddr_servoConfig + idx * sizeof(ServoConfig), *this);
}


void waitAndRefresh(int l, Servo& s1, Servo& s2) {
#ifdef SOFTWARE_SERVO
  long ms = millis();
  long e = ms + l;
  while (millis() < e) {
    delay(5);
    s1.refresh();
    s2.refresh();
  }
#else
  delay(l);
#endif
}

void initServoFeedback(int pos, const ServoConfig& cfg) {
  if (cfg.isEmpty()) {
    return;
  }
  int out = cfg.output();
  if (out < 0) {
    return;
  }
  int l = cfg.left();
  pos -= l;
  bool b = (pos > -3) && (pos < 3);
  output.setBit(out, b);
  setOutputActive(out, b);
}
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

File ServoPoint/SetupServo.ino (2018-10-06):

 
byte setupServoLeft;
byte setupServoRight;
byte setupServoSpeed;
signed char setupServoOutput;

byte servoInputState = 0;
int minValue = 0;
int maxValue = 1000;
byte *valTarget = NULL;
int adjStep = 1;
int lastSelectedNumber;
int selectedNumber;
int typedNumber = -1;
long lastTypedMillis;
boolean shown;
boolean wasCancel;
byte digitCount;

char setupServoIndex = -1;

void startSetupServo(int value) {
    setupServoIndex = value;
    ServoConfig tmp;
    tmp.load(value);
    setupServoLeft = tmp.left();
    setupServoRight = tmp.right();
    setupServoSpeed = tmp.speed();
    setupServoOutput = tmp.output();
//    setupServoConfig = tmp;
    if (debugServo) {      
      Serial.print(F("Configuring ")); Serial.println(setupServoIndex + 1);
    }
    setupState = servoSetLeft;
    processKeyInput = true;
    servoInputState = 0;
    handleInputFinished();
}

void displayCurrent() {
  clearNewCommand();
  Action a1;
  ServoActionData& sd = a1.asServoAction();

  switch (servoInputState) {
    case 0:
    case 1:
    case 2:
      Serial.print(F("Pos: ")); Serial.println(selectedNumber);
      sd.move(setupServoIndex, selectedNumber);
      addNewCommand(a1);
      executor.playNewAction();
      return;
    case 3:
      Serial.print(F("Speed: ")); Serial.println(selectedNumber);
      overrideSpeed = selectedNumber - 1;
      sd.moveLeft(setupServoIndex);
      addNewCommand(a1);
      sd.moveRight(setupServoIndex);
      addNewCommand(a1);
      executor.playNewAction();
      return;
    default:
      return;
  }
}

void handleInputCancelled() {
  enterSetup();
}

void handleInputReset() {
  if (valTarget != NULL) {
    selectedNumber = *valTarget;  
    if (servoInputState >= 3) {
      selectedNumber++;
    }
  }
}

void commitServoInput() {
    setupServoSpeed = selectedNumber - 1;
    overrideSpeed = -1;
    // Persist in EEPROM
    ServoConfig tmp(setupServoLeft, setupServoRight, setupServoSpeed, setupServoOutput);
    tmp.save(setupServoIndex);
    servoEEWriteSetup();
    enterSetup();
}

void handleInputFinished() {
  if (valTarget != NULL) {
    *valTarget = selectedNumber;
  }
  if (debugServo) {
    Serial.print("KIfin:"); Serial.print(selectedNumber); Serial.println(servoInputState);
  }
  switch (servoInputState) {
    case 0:
      minValue = 0;
      maxValue = 180;
      adjStep = ServoConfig::servoPwmStep;
      valTarget = &setupServoLeft;

      Serial.print(F("Adj left: ")); 
      break;
    case 1:
      Serial.print(F("LEFT: ")); Serial.println(selectedNumber);
      minValue = 0;
      maxValue = 180;
      adjStep = ServoConfig::servoPwmStep;
      valTarget = &setupServoRight;

      Serial.print(F("Adj right: ")); 
      break;
    case 2:
      Serial.print(F("RIGHT: ")); Serial.println(selectedNumber);
      minValue = 1;
      maxValue = 8;
      adjStep = 1;
      valTarget = &setupServoSpeed;
  
      Serial.print(F("Adj speed: ")); 
      break;
      
    case 3:
      Serial.print(F("SPEED: ")); Serial.println(selectedNumber);
      commitServoInput();
      return;
    default:
      handleInputCancelled();
      return;
  }
  selectedNumber = *valTarget;
  servoInputState++;
  if (servoInputState >= 3) {
    selectedNumber++;
  }
  Serial.println(selectedNumber);
  lastSelectedNumber = selectedNumber;
  displayCurrent();
}

void handleKeyInput() {
  boolean prevCancel = wasCancel;
  boolean ok = true;

  wasCancel = currentKey == keychar_cancel;
  switch (currentKey) {
    case keychar_cancel:
      if (!prevCancel) {
        Serial.print(F("\nCancel\n"));
        handleInputReset();
        break;
      } else {
        if (debugControl) {
          Serial.print(F("Abort\n"));
        }
        handleInputCancelled();
        return;
      }
    case keychar_plus:
      if (debugServo) {
        Serial.println("KIPlus");
      }
      selectedNumber += adjStep;
      break;
    case keychar_minus:
      if (debugServo) {
        Serial.println("KIMinus");
      }
      selectedNumber -= adjStep;
      break;

    case keychar_ok:
      handleInputFinished();
      return;
  }
  if (selectedNumber > maxValue) {
    selectedNumber = maxValue;
    ok = false;
  } else if (selectedNumber < minValue) {
    selectedNumber = minValue;
    ok = false;
  }
  if (debugServo) {
    Serial.print("KIfin:"); Serial.print(selectedNumber); Serial.println(lastSelectedNumber);
  }
  if (lastSelectedNumber != selectedNumber) {
    displayCurrent();
    lastSelectedNumber = selectedNumber;
  }
}
void rangeCommand() {
  int index = servoNumber();
  int left = nextNumber();
  int right = nextNumber();

  if (index < 1) {
    return;
  }
  if (left < 0 || left > 180 || right < 0 || right > 180) {
    Serial.println(F("\nBad Pos"));
    return;
  }
  index--;

  ServoConfig tmpConfig;

  tmpConfig.load(index);
  int spd = tmpConfig.speed();
  if ((*inputPos) != 0) {
    spd = nextNumber();
    if (spd < 1 || spd > 8) {
      Serial.println(F("\nBad speed"));
      return;
    }
    spd--;
  }
  tmpConfig.setLeft(left);
  tmpConfig.setRight(right);
  tmpConfig.setSpeed(spd);
  
  initPrintBuffer();
  tmpConfig.print(index + 1, printBuffer);
  Serial.println(printBuffer);
  tmpConfig.save(index);
  Serial.println(F("\nOK"));
}

int servoNumber() {
  int index = nextNumber();
  if (index < 1 || index > MAX_SERVO) {
    Serial.print(F("Bad servo")); Serial.println(index);
    return -1;
  }
  return index;
}

void commandServoFeedback() {
  int index = servoNumber();
  int out = nextNumber();
  if (index < 0) {
    return;
  }
  ServoConfig tmp;
  tmp.load(index - 1);
  if (out == -2 || out == 0) {
    tmp.setOutput(-1);
  } else if (out < 0 || out > MAX_OUTPUT) {
    Serial.print(F("Bad output ")); Serial.println(out);
    return;
  } else {
    tmp.setOutput(out - 1);
  }
  tmp.save(index - 1);
  Serial.print(F("Servo ")); Serial.print(index); Serial.print(F(" output ")); Serial.println(out);
}


bool lastNewline;

void commandCalibrate() {
  int idx = servoNumber();
  if (idx < 1) {
    Serial.print(F("Bad servo ")); 
    if (idx >= 0) {
      Serial.println(idx);
    } else {
      Serial.println();
    }
    return;
  }

  setupActive = true;
  Serial.print(F("Calibrate ")); Serial.println(idx);
  Serial.println(F("Use Q +, A -, ENTER/* = OK, SPACE/# = cancel"));
  Serial.print(F("Set LEFT "));
  lastNewline = false;
  charModeCallback = &calibrateTerminalCallback;
  startSetupServo(idx - 1);  
}

void calibrateTerminalCallback(char c) {
  char tr;
  boolean wasNewline = lastNewline;

  lastNewline = false;
  switch (c) {
    case 'q': case 'Q': tr = '+'; break;
    case 'a': case 'A': tr = '-'; break;
    case '\r': case '\n': {
      if (!wasNewline) {
        tr = '*'; 
      }
      lastNewline = true;
      break;
    }
    case 0x7f: case 0x1b: case ' ': tr = '#'; break;

    default:
      tr = c;
      break;
  }
  currentKey = tr;
  setupHandleKey();
}

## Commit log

2018-03-04 Servo configuration stored only in EEPROM, saving 50 byte
2018-03-07 Set latch low so that keyboard may use the clock pin
2018-03-10 More command modes, bugfixes in servo
    [Action.ino, Command.ino, Common.h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]
2018-03-10 Implemented servo feedback
2018-03-10 Servo feedback restored after power on
2018-03-11 Prototype, too much memory consumed
    [Common.h, Defs.h, Output.ino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]
2018-03-12 fixed definition of new range - output is reset
    [Common.h]
2018-03-14 Eagle files
    [servopoinB-2.brd, servopoinB-2.sch]
2018-03-27 Refactored delayed action cancel, bugfixes
    [Command.ino, Common.h, Defs.h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]
2018-03-30 Avoid erroneous unhandled message
    [Command.ino]
2018-03-30 Array loop optimizations. Do not wave servos when idle
2018-03-30 Bugfixes, wait time printed
    [Common.h, Scheduler.ino, Terminal.ino]
2018-03-30 Fixed bugs in scheduler, wait command works
    [Action.ino, Common.h, Processor.ino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]
2018-03-31 Shortened strings, removed excess setup
    [SetupServo.ino]
2018-03-31 Optimized furhter, bugfixes for scheduler, implemented flashing
    [Common.h, Defs.h, Output.ino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]
2018-04-01 Removed sprintfs, replaced by itoa and strcat
    [Action.ino, Command.ino, Common.h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]
2018-04-05 Added missing int > byte conversion
    [Common.h]
2018-04-07 Moved so that Arduino IDE recognizes the sketch
2018-05-16 Verze B3 se svorkovnici
    [servopoinB3.brd, servopoinB3.sch]
